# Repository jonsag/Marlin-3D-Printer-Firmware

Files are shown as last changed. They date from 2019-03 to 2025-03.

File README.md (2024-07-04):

# Marlin 3D Printer Firmware

Everything in this repo is for Geeetech I3 Pro B  

*************
Refer to .md file for the Marlin version you want to use.  

Read that file carefully, PLEASE!
*************

## Marlin firmware for my Geeetech i3 Pro B with GT2560A+ board  

Includes BLTouch, T8 lead screws and RepRap Discount Full Graphic Smart Controller.  

I recommend using VSCode for compiling and uploading to printer.  

## Compilation

I use [VS Code](https://code.visualstudio.com/) with [PlatformIO](https://platformio.org/) and [Auto Build Marlin](https://marlinfw.org/docs/basics/auto_build_marlin.html) for compiling, but you can also do this with [Arduino IDE](https://www.arduino.cc/en/software).  

VS Code/PlatformIO instructions [here](<./VSCode, Installation, Compiling and Uploading.md>).  

## Testing and calibrating

View current settings and parameters  
> M503

### BLTouch

#### Set Z offset

View current offset  
> M851 ; view current Z offset

    Send: M851
    Recv: echo:Probe Z Offset: -0.95
    Recv: ok

Heat up bed
> M140 S75 ; set bed temp to 75

Home all axis
> G28 ; home all axis
>
Disable software end stops  
> M211 S0 ; disable software end stops

Do the paper test and bring down Z slowly.  
Note the Z value.  
> M114 ; get current position

Set new offset  
> M851 Z-0.8

    Send: M851 Z-0.8
    Recv: echo:Probe Z Offset: -0.80
    Recv: ok

Save new value to EEPROM  
> M500

You can also adjust the Z offset during prints.  
Double click the knob and adjust the offset until it's OK.  
Then insert new value as above.  

Higher value -> smaller distance from bed  

#### Sensor test

> M280 P0 S10 ; pushes the pin down  
> M280 P0 S90 ; pulls the pin up  
> M280 P0 S120 ; self test – keeps going until you do pin up/down or release alarm  
> M280 P0 S160 ; release alarm  

### PID Tuning

Check current settings  
> M503 ; print all settings stored in eeprom  

    ...
    Recv: echo:; Hotend PID:
    Recv: echo:  M301 P23.12 I1.72 D77.65
    ...  

#### Hotend PID Tuning

Start parts cooler fan  
> M106 S255 ; set parts fan to 100%  

    Send: M106 S255
    Recv: ok

Start tuning  
> M303 E0 S245 C8 ; tune at 245 degrees 8 times  

    ...
    Recv: PID Autotune finished! Put the last Kp, Ki and Kd constants from below into Configuration.h
    Recv: #define DEFAULT_Kp 17.06
    Recv: #define DEFAULT_Ki 1.05
    Recv: #define DEFAULT_Kd 69.18
    ...

Enter new values  
> M301 P17.06 I1.05 D69.18 ; set hotend PID values  

    Send: M301 P17.06 I1.05 D69.18
    Recv: ok

Save to EEPROM  
> M500 ; store to eeprom  

    Send: M500
    Recv: echo:Settings Stored (627 bytes; crc 55228)
    Recv: ok

Stop parts cooler fan  
> M106 S0 ; turn off parts fan

#### Bed PID Tuning

Start tuning  
> M303 E-1 S75 C8 ; tune at 75 degrees 8 times

    ...
    Recv: #define DEFAULT_bedKp 49.22
    Recv: #define DEFAULT_bedKi 9.39
    Recv: #define DEFAULT_bedKd 172.04
    ...

Enter new values  
> M304 P49.22 I9.39 D172.04 ; set bed PID values  

    Recv: ok

Save to EEPROM  
> M500 ; store to eeprom

### Set temperatures

Set extruder temperature  
> M104 S205 ; set temp for default extruder to 205 degrees  

    Send: M104 S205
    Recv: ok

Set bed temperature  
> M140 S65 ; set bed temp to 65 degrees

    Send: M140 S65
    Recv: ok
    ...

### Steps/mm

Show current settings (steps per mm etc)  
> M501

    echo:V47 stored settings retrieved (614 bytes; crc 29566)
    echo:  G21    ; Units in mm
    echo:  M149 C ; Units in Celsius

    echo:Filament settings: Disabled
    echo:  M200 D1.75
    echo:  M200 D0
    echo:Steps per unit:
    echo:  M92 X81.50 Y81.50 Z400.69 E94.00
    echo:Maximum feedrates (units/s):
    echo:  M203 X400.00 Y400.00 Z2.00 E45.00
    echo:Maximum Acceleration (units/s2):
    echo:  M201 X4000 Y4000 Z40 E4000
    echo:Acceleration (units/s2): P<print_accel> R<retract_accel> T<travel_accel>
    echo:  M204 P3000.00 R3000.00 T3000.00
    echo:Advanced: S<min_feedrate> T<min_travel_feedrate> B<min_segment_time_us> X<max_xy_jerk> Z<max_z_jerk> E<max_e_jerk>
    echo:  M205 S0.00 T0.00 B20000 X10.00 Y10.00 Z0.30 E5.00
    echo:Home offset:
    echo:  M206 X0.00 Y0.00 Z0.00
    echo:Auto Bed Leveling:
    echo:  M420 S0
    echo:Material heatup parameters:
    echo:  M145 S0 H180 B70 F0
    echo:  M145 S1 H215 B105 F0
    echo:PID settings:
    echo:  M301 P22.06 I1.06 D114.78
    echo:Z-Probe Offset (mm):
    echo:  M851 Z-0.61 

### Set X/Y center

Home X and Y axes  
> G28 X Y

Set extruder at 0:0  
> G1 X0 Y0

Set extruder at bed center  
> G1 X95 Y96

if bed size is set to 190x192mm in Configuration.h in Marlin firmware  

    // The size of the print bed
    #define X_BED_SIZE 190
    #define Y_BED_SIZE 192

Compensate with  

    #define X_MIN_POS 0
    #define Y_MIN_POS 0
    ...
    #define X_MAX_POS X_BED_SIZE
    #define Y_MAX_POS Y_BED_SIZE

### Homing and leveling

> G28 ; home all axes
> G29 ; do bed leveling

### Set skew factor

Adapted from [https://github.com/MarlinFirmware/Configurations/blob/import-2.0.x/config/examples/Geeetech/Prusa%20i3%20Pro%20B/bltouch/README.md](https://github.com/MarlinFirmware/Configurations/blob/import-2.0.x/config/examples/Geeetech/Prusa%20i3%20Pro%20B/bltouch/README.md)  

The skew factor must be adjusted for each printer:  

First, uncomment `#define XY_SKEW_FACTOR 0.0`, if commented  

      #define XY_SKEW_FACTOR 0.0

Compile and upload the firmware.  
Then, print [YACS (Yet Another Calibration Square)](https://www.thingiverse.com/thing:2563185).  
Hint: scale it considering a margin for brim (if used). The larger, the better to make error measurements.  
Measure the printed part according to the comments in the example configuration file, and set `XY_DIAG_AC`, `XY_DIAG_BD` and `Y_SIDE_AD`.  

      #define XY_DIAG_AC 282.8427124746
      #define XY_DIAG_BD 282.8427124746
      #define XY_SIDE_AD 200
  
Comment `#define XY_SKEW_FACTOR 0.0` again.  

      //#define XY_SKEW_FACTOR 0.0

Compile and upload again.  

## Permissions

Check your permissions.  
You need to belong to the groups tty and dialout to be able to write to the tty/USBx.  

Run  
>$ groups | grep ' tty ' && echo -e "\nGreat! \nYou are a member of 'tty'" || echo -e "\nError: \nYou are not a member of the group 'tty'. \n\nCorrect with 'sudo usermod -a -G tty $USER'"

and  
>$ groups | grep ' dialout ' && echo -e "\nGreat! \nYou are a member of 'dialout'" || echo -e "\nError: \nYou are not a member of the group 'dialout'. \n\nCorrect with 'sudo usermod -a -G dialout $USER'"

to check.  

If you had to add yourself to any group, you must reboot to join the groups.  

>$ sudo reboot

## avrdude

Install avrdude if not installed.  
>$ sudo apt install avrdude

### Upload binary

>$ avrdude -v -q -p m2560 -c wiring -P /dev/ttyUSB0 -D -U flash:w:/path/to/image.hex:i

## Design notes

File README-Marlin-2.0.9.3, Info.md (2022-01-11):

# Firmware Marlin-2.0.9.3 for Geeetech I3 Pro B

Please scroll through whole document so you don't miss anything. :-)  

## Important note - MUST READ

There is a line you HAVE to change in configuration.h before compiling this.  

Uncomment line to disable my skew correction values.  

    #define XY_SKEW_FACTOR 0.0

Comment these out again after you've made the test print and measurements. Read more below.  

(It's not really a disaster if you forget this, but you will get a more skewed print probably.)  

## Other changes for different setups

Below are changes you have to do, if you have a different setup than I have.  

### IF you DON'T have a BLTouch or clone

Comment out line  

    //#define BLTOUCH

### IF you DON'T have T8 lead screws

Comment out line  

    //#define PRO_B_WITH_LEADSCREW

### IF you have the STOCK LCD screen

Comment out line  

    //#define REPRAP_DISCOUNT_FULL_GRAPHIC_SMART_CONTROLLER

and uncomment line  

    #define REPRAP_DISCOUNT_SMART_CONTROLLER

### If you have a BLTouch or clone, not mounted in the same way I have

Check your probe offsets on line  

    #define NOZZLE_TO_PROBE_OFFSET { xx, yy, -zz }

Check offsets on lines  

    #define PROBING_MARGIN_LEFT xx
    #define PROBING_MARGIN_RIGHT xx
    #define PROBING_MARGIN_FRONT yy
    #define PROBING_MARGIN_BACK yy

Check values on line for the "Level Corners" option  

      #define LEVEL_CORNERS_INSET_LFRB { xx, yy, xx, yy } // (mm) Left, Front, Right, Back insets

## Compilation

I use [VS Code](https://code.visualstudio.com/) with [PlatformIO](https://platformio.org/) and [Auto Build Marlin](https://marlinfw.org/docs/basics/auto_build_marlin.html) for compiling, but you can also do this with [Arduino IDE](https://www.arduino.cc/en/software).

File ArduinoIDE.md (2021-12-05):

# Arduino IDE

## Compiling and uploading on Arduino IDE

Download and install Arduino IDE 1.8.x from [https://www.arduino.cc/en/software](https://www.arduino.cc/en/software)  

Open Arduino IDE and open /path/to/Marlin.ini  

Select board:  
    Tools -> Board: ... -> Arduino AVR Boards -> Arduino 2560 or Mega 2560  

Select processor:  
    Tools -> Processor: ... -> ATmega2560 (Mega 2560)  

Set port:  
    Tools -> /dev/ttyUSB0 (or whatever...)  

Select programmer:  
    Tools -> Programmer: ... -> AVRISP  

Compile and upload!  

## Working with binary files

Instead of directly uploading the compiled code with Arduino IDE you can save the compiled code for later upload.  

### Export firmware to binary

Start Arduino IDE and select file and board as above.  

Click 'Sketch -> Export compiled binary'  

The IDE now compiles the firmware to a binary file in the same location as your Marlin.ini.  
It will be called Marlin.ino.mega.hex  

Move the file, and rename it to something sensible.

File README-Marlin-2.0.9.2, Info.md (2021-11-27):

# Firmware Marlin-2.0.9.2 for Geeetech I3 Pro B

Please scroll through whole document so you don't miss anything. :-)  

## Important note - MUST READ

There is a line you HAVE to change in configuration.h before compiling this.  

Uncomment line 1805 to disable my skew correction values.  

    #define XY_SKEW_FACTOR 0.0

Comment these out again after you've made the test print and measurements. Read more below.  

(It's not really a disaster if you forget this, but you will get a more skewed print probably.)  

## Other changes for different setups

Below are changes you have to do, if you have a different setup than I have.  

### IF you DON'T have a BLTouch or clone

Comment out line 1095  

    //#define BLTOUCH

### IF you DON'T have T8 lead screws

Comment out line 930  

    //#define PRO_B_WITH_LEADSCREW

### IF you have the STOCK LCD screen

Comment out line 2376  

    //#define REPRAP_DISCOUNT_FULL_GRAPHIC_SMART_CONTROLLER

and uncomment line 2218  

    #define REPRAP_DISCOUNT_SMART_CONTROLLER

### If you have a BLTouch or clone, not mounted in the same way I have

Check your probe offsets on line 1190  

    #define NOZZLE_TO_PROBE_OFFSET { xx, yy, -zz }

Check offsets on lines 1195-  

    #define PROBING_MARGIN_LEFT xx
    #define PROBING_MARGIN_RIGHT xx
    #define PROBING_MARGIN_FRONT yy
    #define PROBING_MARGIN_BACK yy

Check values on line 1694 for the "Level Corners" option  

      #define LEVEL_CORNERS_INSET_LFRB { xx, yy, xx, yy } // (mm) Left, Front, Right, Back insets

## Compilation

I use [VS Code](https://code.visualstudio.com/) with [PlatformIO](https://platformio.org/) and [Auto Build Marlin](https://marlinfw.org/docs/basics/auto_build_marlin.html) for compiling, but you can also do this with [Arduino IDE](https://www.arduino.cc/en/software).  

## Misc g-code

### Settings

>M503 ; view current settings and parameters
>M500 ; store settings to EEPROM
>M502 ; load settings from EEPROM

### BLTouch

>M280 P0 S10 ; pushes the pin down  
>M280 P0 S90 ; pulls the pin up  
>M280 P0 S120 ; Self test – keeps going until you do pin up/down or release alarm  
>M280 P0 S160 ; Release alarm  

### Homing and leveling

>G28 ; home all axes
>G29 ; do bed leveling

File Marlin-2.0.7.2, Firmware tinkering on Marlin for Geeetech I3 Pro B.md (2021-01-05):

## Firmware tinkering on Marlin-2.0.7.2 for Geeetech I3 Pro B

Further down in this document are instructions on how to trim, set up and install firmware on your printer.  

Please scroll through whole document so you don't miss anything. :-)  

Instructions below are run on a Linux system.  

Important note - MUST READ
==========
There is line you HAVE to change in configuraton.h before compiling this.  

Uncomment line 1454 to disable my skew correction values.  

	#define XY_SKEW_FACTOR 0.0
	
Comment these out again after you've made the test print and measurements. Read more below.  

(It's not really a disaster if you forget this, but you will get a more skewed print probably.)

Other changes for different setups
==========
Below are changes you have to do, if you have a different setup than I have.  

IF you DON'T have a BLTouch or clone
----------
Comment out line 907

	//#define BLTOUCH
	
IF you DON'T have T8 lead screws
----------
Comment out line 744  

	//#define PRO_B_WITH_LEADSCREW
	
IF you have the STOCK LCD screen
---------
Comment out line 2000  

	//#define REPRAP_DISCOUNT_FULL_GRAPHIC_SMART_CONTROLLER
	
and uncomment line 1850  

	#define REPRAP_DISCOUNT_SMART_CONTROLLER
	
If you have a BLTouch or clone, not mounted in the same way I have
----------
Check your probe offsets on line 997  

	#define NOZZLE_TO_PROBE_OFFSET { xx, yy, -zz }
	
Check offsets on lines 1002-  

	#define PROBING_MARGIN_LEFT xx
	#define PROBING_MARGIN_RIGHT xx
	#define PROBING_MARGIN_FRONT yy
	#define PROBING_MARGIN_BACK yy

Check values on line 1386 for the "Level Corners" option  

	  #define LEVEL_CORNERS_INSET_LFRB { xx, yy, xx, yy } // (mm) Left, Front, Right, Back insets

Changes from original firmware release
==========
These are my changes from the source firmware.  
Some things will perhaps have to be adapted to fit your printer setup.  

Makefile
----------
Line 62  

	HARDWARE_MOTHERBOARD ?= 1315
  
>Perhaps not really necessary, but this setting reflects the hardware.
  
configuration.h
----------
Line 73  

	#define STRING_CONFIG_H_AUTHOR "jonsag" // Who made the changes.

> My little mark.
	
130  

	  #define MOTHERBOARD BOARD_GT2560_REV_A_PLUS

>This is essential. Points directly to our hardware setup.
	
134  

	#define CUSTOM_MACHINE_NAME "Geeetech i3 Pro B"

>Puts some text on the display at startup.

426  

	#define TEMP_SENSOR_BED 1
	
>Defines that we have a heated bed, and what type of thermistor.

476  

	#define BED_MAXTEMP      125

>Sets maximum temperature for the heated bed.

498-  

	    #define DEFAULT_Kp_LIST {  22.39,  22.39 }
	    #define DEFAULT_Ki_LIST {   1.91,   1.91 }
	    #define DEFAULT_Kd_LIST { 65.58, 65.58 }

>These are not really used, since we only have one hotend.

502-  

	    #define DEFAULT_Kp  23.12
	    #define DEFAULT_Ki   1.72
	    #define DEFAULT_Kd 77.65

>These are the PID constants that will be used. However I recommend you do a PID tuning as later described.

596  

	//#define THERMAL_PROTECTION_CHAMBER // Enable thermal protection for the heated chamber
	
>If you have a heated and monitored chamber you should uncomment this.

681-  

	#define X_DRIVER_TYPE  A4988
	#define Y_DRIVER_TYPE  A4988
	#define Z_DRIVER_TYPE  A4988

>Not necessary to uncomment, but this now reflects the stock Geeetech drivers.

689  

	#define E0_DRIVER_TYPE A4988

>See above.	

744-  

	#define PRO_B_WITH_LEADSCREW
	#if ENABLED(PRO_B_WITH_LEADSCREW)       // T8 leadscrew version
	  #define DEFAULT_AXIS_STEPS_PER_UNIT   { 81.5, 81.5, 400.69, 108 }
	#else                                   // M8 threaded rod version
	  #define DEFAULT_AXIS_STEPS_PER_UNIT   { 78.74, 78.74, 2560, 105 }
	#endif

> Z steps for T8 lead screws. The added lines are just for conveniance.
	
756  

	#define DEFAULT_MAX_FEEDRATE          { 400, 400, 2, 45 }

>Recommended values. Could be tweaked.

769  

	#define DEFAULT_MAX_ACCELERATION      { 5000, 5000, 50, 5000 }

>See above.

784-  

	#define DEFAULT_ACCELERATION          1000    // X, Y, Z and E acceleration for printing moves
	#define DEFAULT_RETRACT_ACCELERATION  2000    // E acceleration for retracts
	#define DEFAULT_TRAVEL_ACCELERATION   1000    // X, Y, Z acceleration for travel (non printing) moves

>See above.

798  

	 #define DEFAULT_XJERK                 20.0
	 #define DEFAULT_YJERK                 20.0
	 #define DEFAULT_ZJERK                 0.4
  
  >If you enable CLASSIC_JERK on line 796, these are recommended values.  Could be tweaked, but not used now.
  
833  

	#define S_CURVE_ACCELERATION
	
>Better acceleration curve.
	
907-  

	#define BLTOUCH
	#if ENABLED(BLTOUCH)
	  #define BLTOUCH_DELAY 375   // (ms) Enable and increase if 	needed
	#endif

>Essential for BLTouch, and it's clones. Also sets delay.

997  

	#define NOZZLE_TO_PROBE_OFFSET { 20, 2, -0.9}
>The BLTouch's offset from the nozzle. Change these to match your setup.

1002-  

	#define PROBING_MARGIN_LEFT 60
	#define PROBING_MARGIN_RIGHT 0
	#define PROBING_MARGIN_FRONT 0
	#define PROBING_MARGIN_BACK 0

>With these settings I avoid interfering with the clips holding down the glass plate.

1054  

	#define Z_MIN_PROBE_REPEATABILITY_TEST
	
>Enables testing of the repeatability of the level probe.

1101  

	#define INVERT_X_DIR true

>Necessary for our hardware.

1108  

	#define INVERT_E0_DIR true

>See above.
	
1137-  

	#define X_BED_SIZE 186
	#define Y_BED_SIZE 167

>We could adjust this, but now I avoid interferring with the glass bed clamps.
	
1141-  

	#define X_MIN_POS 10
	#define Y_MIN_POS -10

>See above.

1144-  

	#define X_MAX_POS (X_MIN_POS + X_BED_SIZE)
	#define Y_MAX_POS (-Y_MIN_POS + Y_BED_SIZE))
	#define Z_MAX_POS 185

>This is the conclusion of the above settings.
	
1248  

	#define AUTO_BED_LEVELING_LINEAR
	
>You could also uncomment line 1249 instead, or one of the other measurement types. This makes most sense to me.
	
1257  

	#define RESTORE_LEVELING_AFTER_G28
	
>Keeps the leveling data after a G28 home command.

1296  

	#define GRID_MAX_POINTS_X 3
	
>The number of probes in both directions. The value squared is the total number of probes.

1306  

	#define EXTRAPOLATE_BEYOND_GRID

>If you went with bilinear probong above, this is a good setting.
 
1326  

	  #define MESH_EDIT_GFX_OVERLAY   // Display a graphics overlay while editing the mesh

>For unified bed leveling this is a nice feature.

1356  

	#define LCD_BED_LEVELING

>Adds an extra option on how to level the bed.
	
1365  

	#define LEVEL_BED_CORNERS

>A nice feature for do some basic manual leveling.
 
1368  

	  #define LEVEL_CORNERS_INSET_LFRB { 35, 10, 15, 20 } // (mm) Left, Front, Right, Back insets

>Keeps the hotend away from the clamps.

1371  

	  #define LEVEL_CENTER_TOO              // Move to the center after the last corner

>Stop at center when doing the corners.
 
1400  

	#define Z_SAFE_HOMING

>Don't let the probe get outside the bed.
	
1444  

	#define SKEW_CORRECTION

>Enabling this lets your firmware make correctionsto your printer setup. If your axes are not completely perpendicular to each other, which they seldom are, these will be corrected. Read below on how to do this.

1448  

	  #define XY_DIAG_AC 143.55 //142.90 // should be 143.754808615 //282.8427124746
	  #define XY_DIAG_BD 143.95 //143.10 //282.8427124746
	  #define XY_SIDE_AD 101.65
  
>These are MY values AFTER I've done the test print and measuring. You will have enter YOUR values.

1454  

	  //#define XY_SKEW_FACTOR 0.0
	  
>Comment this AFTER you've done the test print and measurements.
 
1468  

	  #define SKEW_CORRECTION_GCODE

>Extra feature for skew correction.
 
1486-  

	#define EEPROM_SETTINGS     // Persistent storage with M500 and M501

>Enables storing of settings with G-code.
	
1518  

	#define PREHEAT_1_TEMP_HOTEND 200
	#define PREHEAT_1_TEMP_BED     65

>Enter whatever values are handy for you.
	
1522  

	#define PREHEAT_2_LABEL       "PETG"
	#define PREHEAT_2_TEMP_HOTEND 235
	#define PREHEAT_2_TEMP_BED    85

>See above.

1739  

	#define SDSUPPORT

>We do have an SD card reader.

1756  

	#define SD_CHECK_AND_RETRY

>This setting makes sense.

1819  

	#define INDIVIDUAL_AXIS_HOMING_MENU

>Handy option to have.
	
1827  

	#define SPEAKER

>Our speaker is capable of putting out some different sounds.

1836-  

	#define LCD_FEEDBACK_FREQUENCY_DURATION_MS 4
	#define LCD_FEEDBACK_FREQUENCY_HZ 5000

>I think button press beeps are nice.

2000  

	#define REPRAP_DISCOUNT_SMART_CONTROLLER

>I have upgraded my printer with this full graphic LCD. If you still have the stock control panel, enable line 1850 instead.
	
Other possible changes in configuration.h
==========

Extra probing
----------
1025  

	#define MULTIPLE_PROBING 3

Compiling and uploading on Arduino IDE
==========
Download and install Arduino IDE 1.8.x from https://www.arduino.cc/en/software  

Open Arduino IDE and open /path/to/Marlin.ini  

Select board:  
Tools -> Board: ... -> Arduino AVR Boards -> Arduino 2560 or Mega 2560  

Select processor:  
Tools -> Processor: ... -> ATmega2560 (Mega 2560)  
 
 Set port:  
Tools -> /dev/ttyUSB0 or whatever...  

Select programmer:  
Tools -> Programmer: ... -> AVRIPS mkII  

Compile and upload!  

Permissions
==========
Check your permissions. You need to belong to the groups tty and dialout to be able to write to the tty/USB.  

Run  
>$ groups | grep ' tty ' && echo -e "\nGreat! \nYou are a member of 'tty'" || echo -e "\nError: \nYou are not a member of the group 'tty'. \n\nCorrect with 'sudo usermod -a -G tty $USER'"

and  
>$ groups | grep ' dialout ' && echo -e "\nGreat! \nYou are a member of 'dialout'" || echo -e "\nError: \nYou are not a member of the group 'dialout'. \n\nCorrect with 'sudo usermod -a -G dialout $USER'"

to check.  

If you had to add yourself to any group, you must reboot to join the groups.  

>$ sudo reboot

Working with binary files
==========
Instead of directly uploading the compiled code with Arduino IDE you can save the compiled code for later upload.  

Export firmware to binary
----------
 Start Arduino IDE and select file and board as above.  

Click 'Sketch -> Export compiled binary'  

The IDE now compiles the firmware to a binary file in the same location as your Marlin.ini.  
It will be called Marlin.ino.mega.hex  

Move the file, and rename it to something sensible.  

avrdude
----------
Install avrdude if not installed.  
>$ sudo apt install avrdude

avrdude is already a part of the Arduino IDE, but this makes it easier to run.  

Upload binary
----------
>$ avrdude -v -q -p m2560 -c wiring -P /dev/ttyUSB0 -D -U flash:w:/path/to/image.hex:i

Configuration after upload
==========

PID tuning
---------------
Start parts fan at 100%  
>M106 S255

	[...]
	Send: M106 S255
	Recv: ok
	[...]

Start tuning  
>M303 E0 S205 C8

	[...]
	Recv:  bias: 169 d: 85 min: 202.71 max: 207.81 Ku: 42.41 Tu: 27.20
	Recv:  Classic PID
	Recv:  Kp: 25.44 Ki: 1.87 Kd: 86.50
	Recv: PID Autotune finished! Put the last Kp, Ki and Kd constants from below into Configuration.h
	Recv: #define DEFAULT_Kp 25.44
	Recv: #define DEFAULT_Ki 1.87
	Recv: #define DEFAULT_Kd 86.50
	Recv: ok
	[...]
	
Enter new values  
>M301 P25.44 I1.87 D86.50

	[...]
	Send: M301 P25.44 I1.87 D86.50
	Recv: echo: p:25.44 i:1.87 d:86.50
	Recv: ok
	[...]
	
Save to EEPROM  
>M500

	[...]
	Send: M500
	Recv: echo:Settings Stored (657 bytes; crc 43001)
	Recv: ok
	[...]

Set Z-offset
---------------
View current offset  
>M851

	[...]
	Send: M851
	Recv: Probe Offset X20.00 Y2.00 Z-0.90
	Recv: ok
	[...]
	
Set new Z offset  
>M851 Z-0.8

	[...]
	Send: M851 Z-0.8
	Recv: echo:Probe Z Offset: -0.80
	Recv: ok
	[...]
		
Save new value to EEPROM  
>M500

Higher value -> smaller distance from bed  
The above example will decrease the distance from the bed, ie. the gap between nozzle and bed will be smaller.  

This can of course also be done from the LCD-display.  

Skew factor
----------
Adapted from https://github.com/MarlinFirmware/Configurations/blob/import-2.0.x/config/examples/Geeetech/Prusa%20i3%20Pro%20B/bltouch/README.md  

The skew factor must be adjusted for each printer:

- First, uncomment `#define XY_SKEW_FACTOR 0.0`, if commented

1445  

	  #define XY_SKEW_FACTOR 0.0

- Compile and upload the firmware.
- Then, print [YACS (Yet Another Calibration Square)](https://www.thingiverse.com/thing:2563185). Hint, scale it considering a margin for brim (if used). The larger, the better to make error measurements.
- Measure the printed part according to the comments in the example configuration file, and set `XY_DIAG_AC`, `XY_DIAG_BD` and `Y_SIDE_AD`.

1439  

	  #define XY_DIAG_AC 282.8427124746
	  #define XY_DIAG_BD 282.8427124746
	  #define XY_SIDE_AD 200
	  
- Comment `#define XY_SKEW_FACTOR 0.0` again.
	
1445  

	  //#define XY_SKEW_FACTOR 0.0

- Compile and upload again.

Misc g-code
==========
Settings
----------
>M503 ; view current settings and parameters

>M500 ; store settings to EEPROM

>M502 ; load settings from EEPROM

BLTouch
---------------
>M280 P0 S10 ; pushes the pin down  

>M280 P0 S90 ; pulls the pin up  

>M280 P0 S120 ; Self test – keeps going until you do pin up/down or release alarm  

>M280 P0 S160 ; Release alarm  

Homing and leveling
----------
>G28 ; home all axes

>G29 ; do bed leveling

Below is just for my own reference
==========
Other PID values I've tried:  
>M301 P32.86 I2.59 D104.31 ; 1.1.8, with fan off
>M301 P33.26 I2.49 D111.03 ; 2.0.7.2, with fan off
>M301 P28.44 I2.12 D95.53 ; 2.0.7.2, fan on
>M301 P23.26 I1.72 D78.61 ; 2.0.7.2, fan off, 200 degrees
>M301 P23.12 I1.72 D77.65 ; 2.0.7.2, fan on, 200 degrees

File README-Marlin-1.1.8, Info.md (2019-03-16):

#Firmware tinkering on Marlin for Geeetech I3 Pro B

Configuration.h
===============

Motherboard selection, 119-123
---------------
	// The following define selects which electronics board you have.
	// Please choose the name from boards.h that matches your setup
	#ifndef MOTHERBOARD
	  #define MOTHERBOARD BOARD_GT2560_REV_A_PLUS
	#endif
	
Custom name, 125-127
---------------
	// Optional custom name for your RepStrap or other custom machine
	// Displayed in the LCD "Ready" message
	#define CUSTOM_MACHINE_NAME "Geeetech i3 Pro B"

Filament diameter, 139-140
---------------
	// Generally expected filament diameter (1.75, 2.85, 3.0, ...). Used for Volumetric, Filament Width Sensor, etc.
	#define DEFAULT_NOMINAL_FILAMENT_DIA 1.75

Temperature sensors, 243-294
---------------
	/**
	 * --NORMAL IS 4.7kohm PULLUP!-- 1kohm pullup can be used on hotend sensor, using correct resistor and table
	 *
	 * Temperature sensors available:
	...
	...
	...
	 */
	#define TEMP_SENSOR_0 1
	#define TEMP_SENSOR_1 0
	#define TEMP_SENSOR_2 0
	#define TEMP_SENSOR_3 0
	#define TEMP_SENSOR_4 0
	#define TEMP_SENSOR_BED 1
	
Min temps, 315-323
---------------
	// The minimal temperature defines the temperature below which the heater will not be enabled It is used
	// to check that the wiring to the thermistor is not broken.
	// Otherwise this would lead to the heater being powered on all the time.
	#define HEATER_0_MINTEMP 8
	#define HEATER_1_MINTEMP 5
	#define HEATER_2_MINTEMP 5
	#define HEATER_3_MINTEMP 5
	#define HEATER_4_MINTEMP 5
	#define BED_MINTEMP 8

Steps/mm, 527-533
---------------
	/**
	 * Default Axis Steps Per Unit (steps/mm)
	 * Override with M92
	 *                                      X, Y, Z, E0 [, E1[, E2[, E3[, E4]]]]
	 */
	//#define DEFAULT_AXIS_STEPS_PER_UNIT   { 81.5, 81.5, 2577.46, 94 }
	#define DEFAULT_AXIS_STEPS_PER_UNIT   { 81.5, 81.5, 400.69, 93 }

Max feed rate, 534-539
---------------
	/**
	 * Default Max Feed Rate (mm/s)
	 * Override with M203
	 *                                      X, Y, Z, E0 [, E1[, E2[, E3[, E4]]]]
	 */
	#define DEFAULT_MAX_FEEDRATE          { 400, 400, 2, 45 }

Max accceleration, 541-547
---------------
	/**
	 * Default Max Acceleration (change/s) change = mm/s
	 * (Maximum start speed for accelerated moves)
	 * Override with M201
	 *                                      X, Y, Z, E0 [, E1[, E2[, E3[, E4]]]]
	 */
	#define DEFAULT_MAX_ACCELERATION      { 5000, 5000, 50, 5000 }

Default acceleration, 549-559
---------------
	/**
	 * Default Acceleration (change/s) change = mm/s
	 * Override with M204
	 *
	 *   M204 P    Acceleration
	 *   M204 R    Retract Acceleration
	 *   M204 T    Travel Acceleration
	 */
	#define DEFAULT_ACCELERATION          1000    // X, Y, Z and E acceleration for printing moves
	#define DEFAULT_RETRACT_ACCELERATION  2000    // E acceleration for retracts
	#define DEFAULT_TRAVEL_ACCELERATION   1000    // X, Y, Z acceleration for travel (non printing) moves

Default jerk, 572-561
---------------
	/**
	 * Default Jerk (mm/s)
	 * Override with M205 X Y Z E
	 *
	 * "Jerk" specifies the minimum speed change that requires acceleration.
	 * When changing speed and direction, if the difference is less than the
	 * value set here, it may happen instantaneously.
	 */
	#define DEFAULT_XJERK                 20.0
	#define DEFAULT_YJERK                 20.0
	#define DEFAULT_ZJERK                  0.4
	#define DEFAULT_EJERK                  5.0
	
Bltouch, 637-643
---------------
	/**
	 * The BLTouch probe uses a Hall effect sensor and emulates a servo.
	 */
	#define BLTOUCH
	#if ENABLED(BLTOUCH)
	  #define BLTOUCH_DELAY 375   // (ms) Enable and increase if needed
	#endif

Bltouch probe offsets, 667-688
---------------
	/**
	 *   Z Probe to nozzle (X,Y) offset, relative to (0, 0).
	 *   X and Y offsets must be integers.
	 *
	 *   In the following example the X and Y offsets are both positive:
	 *   #define X_PROBE_OFFSET_FROM_EXTRUDER 10
	 *   #define Y_PROBE_OFFSET_FROM_EXTRUDER 10
	 *
	 *      +-- BACK ---+
	 *      |           |
	 *    L |    (+) P  | R <-- probe (20,20)
	 *    E |           | I
	 *    F | (-) N (+) | G <-- nozzle (10,10)
	 *    T |           | H
	 *      |    (-)    | T
	 *      |           |
	 *      O-- FRONT --+
	 *    (0,0)
	 */
	#define X_PROBE_OFFSET_FROM_EXTRUDER -40  // X offset: -left  +right  [of the nozzle]
	#define Y_PROBE_OFFSET_FROM_EXTRUDER -0  // Y offset: -front +behind [the nozzle]
	#define Z_PROBE_OFFSET_FROM_EXTRUDER -0.9  // Z offset: -below +above  [the nozzle]

Z clearance, 704-719
---------------
	/**
	 * Z probes require clearance when deploying, stowing, and moving between
	 * probe points to avoid hitting the bed and other hardware.
	 * Servo-mounted probes require extra space for the arm to rotate.
	 * Inductive probes need space to keep from triggering early.
	 *
	 * Use these settings to specify the distance (mm) to raise the probe (or
	 * lower the bed). The values set here apply over and above any (negative)
	 * probe Z Offset set with Z_PROBE_OFFSET_FROM_EXTRUDER, M851, or the LCD.
	 * Only integer values >= 1 are valid here.
	 *
	 * Example: `M851 Z-5` with a CLEARANCE of 4  =>  9mm from bed to nozzle.
	 *     But: `M851 Z+1` with a CLEARANCE of 2  =>  2mm from bed to nozzle.
	 */
	#define Z_CLEARANCE_DEPLOY_PROBE   5 // Z Clearance for Deploy/Stow
	#define Z_CLEARANCE_BETWEEN_PROBES  5 // Z Clearance between probe point
	
Stepper directions, 750-765
---------------
		// Invert the stepper direction. Change (or reverse the motor connector) if an axis goes the wrong way.
	#define INVERT_X_DIR true
	#define INVERT_Y_DIR true
	#define INVERT_Z_DIR false

	// Enable this option for Toshiba stepper drivers
	//#define CONFIG_STEPPERS_TOSHIBA

	// @section extruder

	// For direct drive extruder v9 set to true, for geared extruder set to false.
	#define INVERT_E0_DIR true
	#define INVERT_E1_DIR false
	#define INVERT_E2_DIR false
	#define INVERT_E3_DIR false
	#define INVERT_E4_DIR false
	
Bed size and travel limits, 782-792
---------------

	// The size of the print bed
	#define X_BED_SIZE 196
	#define Y_BED_SIZE 192

	// Travel limits (mm) after homing, corresponding to endstop positions.
	#define X_MIN_POS 5
	#define Y_MIN_POS 0
	#define Z_MIN_POS 0
	#define X_MAX_POS X_BED_SIZE + X_MIN_POS
	#define Y_MAX_POS Y_BED_SIZE
	#define Z_MAX_POS 185
	
Bed levelling, 839-876
---------------
	/**
	 * Choose one of the options below to enable G29 Bed Leveling. The parameters
	 * and behavior of G29 will change depending on your selection.
	 *
	 *  If using a Probe for Z Homing, enable Z_SAFE_HOMING also!
	...
	...
	...
	//#define AUTO_BED_LEVELING_3POINT
	#define AUTO_BED_LEVELING_LINEAR
	//#define AUTO_BED_LEVELING_BILINEAR
	//#define AUTO_BED_LEVELING_UBL
	//#define MESH_BED_LEVELING

Bed levelling options, 912-923
---------------

	  // Set the number of grid points per dimension.
	  #define GRID_MAX_POINTS_X 3
	  #define GRID_MAX_POINTS_Y GRID_MAX_POINTS_X

	  // Set the boundaries for probing (where the probe can reach).
	  #define LEFT_PROBE_BED_POSITION 10
	  #define RIGHT_PROBE_BED_POSITION 150
	  #define FRONT_PROBE_BED_POSITION 10
	  #define BACK_PROBE_BED_POSITION 190

	  // The Z probe minimum outer margin (to validate G29 parameters).
	  #define MIN_PROBE_EDGE 8

Move between bed corners, 1004-1005
---------------
	// Add a menu item to move between bed corners for manual bed adjustment
	#define LEVEL_BED_CORNERS

Z safe homing, 1025-1034
---------------
	// Use "Z Safe Homing" to avoid homing with a Z probe outside the bed area.
	//
	// With this feature enabled:
	//
	// - Allow Z homing only after X and Y homing AND stepper drivers still enabled.
	// - If stepper drivers time out, it will need X and Y homing again before Z homing.
	// - Move the Z probe (or nozzle) to a defined XY point before Z Homing when homing all axes (G28).
	// - Prevent Z homing when the Z probe is outside bed area.
	//
	#define Z_SAFE_HOMING

M500 and M501 commands, 1111-1118
---------------
	// The microcontroller can store settings in the EEPROM, e.g. max velocity...
	// M500 - stores parameters in EEPROM
	// M501 - reads parameters from EEPROM (if you need reset them after you changed them temporarily).
	// M502 - reverts to the default "factory settings".  You still need to store them in EEPROM afterwards if you want to.
	//
	#define EEPROM_SETTINGS // Enable for M500 and M501 commands

Preheating, 1147-1154
---------------
	// Preheat Constants
	#define PREHEAT_1_TEMP_HOTEND 180
	#define PREHEAT_1_TEMP_BED     70
	#define PREHEAT_1_FAN_SPEED     0 // Value from 0 to 255

	#define PREHEAT_2_TEMP_HOTEND 225
	#define PREHEAT_2_TEMP_BED    90
	#define PREHEAT_2_FAN_SPEED     0 // Value from 0 to 255

SD support, 1325-1332
---------------
	/**
	 * SD CARD
	 *
	 * SD Card support is disabled by default. If your controller has an SD slot,
	 * you must uncomment the following option or it won't work.
	 *
	 */
	#define SDSUPPORT

Feedback sound, 1405-1413
---------------
	//
	// The duration and frequency for the UI feedback sound.
	// Set these to 0 to disable audio feedback in the LCD menus.
	//
	// Note: Test audio output with the G-Code:
	//  M300 S<frequency Hz> P<duration ms>
	//
	#define LCD_FEEDBACK_FREQUENCY_DURATION_MS 0
	#define LCD_FEEDBACK_FREQUENCY_HZ 0

Smart controller, 1464-1470
---------------
	//
	// RepRapDiscount Smart Controller.
	// http://reprap.org/wiki/RepRapDiscount_Smart_Controller
	//
	// Note: Usually sold with a white PCB.
	//
	#define REPRAP_DISCOUNT_SMART_CONTROLLER

Marlin_main.cpp
===============

Line 13206
---------------
	        planner.buffer_line(delta[A_AXIS], delta[B_AXIS], raw[Z_AXIS], raw[E_AXIS], _feedrate_mm_s, active_extruder);

Version.h
===============

pins_GT2560_REV_A_PLUS.h
===============

Bltouch, 31-35
---------------
	#if ENABLED(BLTOUCH)
	  #define SERVO0_PIN  11
	#else
	  #define SERVO0_PIN  11
	#endif

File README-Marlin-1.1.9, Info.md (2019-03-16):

#Firmware tinkering on Marlin for Geeetech I3 Pro B

Configuration.h
===============

Motherboard selection, 131-135
---------------
	// The following define selects which electronics board you have.
	// Please choose the name from boards.h that matches your setup
	#ifndef MOTHERBOARD
	  #define MOTHERBOARD BOARD_GT2560_REV_A_PLUS
	#endif
	
Custom name, 137-139
---------------
	// Optional custom name for your RepStrap or other custom machine
	// Displayed in the LCD "Ready" message
	#define CUSTOM_MACHINE_NAME "Geeetech I3 Pro B""

Filament diameter, 151-152
---------------
	// Generally expected filament diameter (1.75, 2.85, 3.0, ...). Used for Volumetric, Filament Width Sensor, etc.
	#define DEFAULT_NOMINAL_FILAMENT_DIA 1.75

Temperature sensors, 264-319
---------------
	/**
	 * --NORMAL IS 4.7kohm PULLUP!-- 1kohm pullup can be used on hotend sensor, using correct resistor and table
	 *
	 * Temperature sensors available:
	...
	...
	...
	 */
	#define TEMP_SENSOR_0 1
	#define TEMP_SENSOR_1 0
	#define TEMP_SENSOR_2 0
	#define TEMP_SENSOR_3 0
	#define TEMP_SENSOR_4 0
	#define TEMP_SENSOR_BED 1
	#define TEMP_SENSOR_CHAMBER 0
	
Min temps, 340-348
---------------
	// The minimal temperature defines the temperature below which the heater will not be enabled It is used
	// to check that the wiring to the thermistor is not broken.
	// Otherwise this would lead to the heater being powered on all the time.
	#define HEATER_0_MINTEMP 8
	#define HEATER_1_MINTEMP 5
	#define HEATER_2_MINTEMP 5
	#define HEATER_3_MINTEMP 5
	#define HEATER_4_MINTEMP 5
	#define BED_MINTEMP 8

Steps/mm, 606-611
---------------
	/**
	 * Default Axis Steps Per Unit (steps/mm)
	 * Override with M92
	 *                                      X, Y, Z, E0 [, E1[, E2[, E3[, E4]]]]
	 */
	#define DEFAULT_AXIS_STEPS_PER_UNIT   { 81.5, 81.5, 400.69, 108 }
	
Max feed rate, 613-618
---------------
	/**
	 * Default Max Feed Rate (mm/s)
	 * Override with M203
	 *                                      X, Y, Z, E0 [, E1[, E2[, E3[, E4]]]]
	 */
	#define DEFAULT_MAX_FEEDRATE          { 400, 400, 2, 45 }
	
Max accceleration, 620-626
---------------
	/**
	 * Default Max Acceleration (change/s) change = mm/s
	 * (Maximum start speed for accelerated moves)
	 * Override with M201
	 *                                      X, Y, Z, E0 [, E1[, E2[, E3[, E4]]]]
	 */
	#define DEFAULT_MAX_ACCELERATION      { 5000, 5000, 50, 5000 }
	
Default acceleration, 628-638
---------------
	/**
	 * Default Acceleration (change/s) change = mm/s
	 * Override with M204
	 *
	 *   M204 P    Acceleration
	 *   M204 R    Retract Acceleration
	 *   M204 T    Travel Acceleration
	 */
	#define DEFAULT_ACCELERATION          1000    // X, Y, Z and E acceleration for printing moves
	#define DEFAULT_RETRACT_ACCELERATION  2000    // E acceleration for retracts
	#define DEFAULT_TRAVEL_ACCELERATION   1000    // X, Y, Z acceleration for travel (non printing) moves

Default jerk, 640-651
---------------
	/**
	 * Default Jerk (mm/s)
	 * Override with M205 X Y Z E
	 *
	 * "Jerk" specifies the minimum speed change that requires acceleration.
	 * When changing speed and direction, if the difference is less than the
	 * value set here, it may happen instantaneously.
	 */
	#define DEFAULT_XJERK                 20.0
	#define DEFAULT_YJERK                 20.0
	#define DEFAULT_ZJERK                 0.4
	#define DEFAULT_EJERK                 5.0
	
Bltouch, 727-733
---------------
	/**
	 * The BLTouch probe uses a Hall effect sensor and emulates a servo.
	 */
	#define BLTOUCH
	#if ENABLED(BLTOUCH)
	  #define BLTOUCH_DELAY 375   // (ms) Enable and increase if needed
	#endif

Bltouch probe offsets, 760-781
---------------	
	/**
	 *   Z Probe to nozzle (X,Y) offset, relative to (0, 0).
	 *   X and Y offsets must be integers.
	 *
	 *   In the following example the X and Y offsets are both positive:
	 *   #define X_PROBE_OFFSET_FROM_EXTRUDER 10
	 *   #define Y_PROBE_OFFSET_FROM_EXTRUDER 10
	 *
	 *      +-- BACK ---+
	 *      |           |
	 *    L |    (+) P  | R <-- probe (20,20)
	 *    E |           | I
	 *    F | (-) N (+) | G <-- nozzle (10,10)
	 *    T |           | H
	 *      |    (-)    | T
	 *      |           |
	 *      O-- FRONT --+
	 *    (0,0)
	 */
	#define X_PROBE_OFFSET_FROM_EXTRUDER -40  // X offset: -left  +right  [of the nozzle]
	#define Y_PROBE_OFFSET_FROM_EXTRUDER 0  // Y offset: -front +behind [the nozzle]
	#define Z_PROBE_OFFSET_FROM_EXTRUDER -0.9   // Z offset: -below +above  [the nozzle]

Speed between probes, 786-787
---------------
	// X and Y axis travel speed (mm/m) between probes
	#define XY_PROBE_SPEED 8000

Feedrate for probing, 792-793
---------------
	// Feedrate (mm/m) for the "accurate" probe of each point
	#define Z_PROBE_SPEED_SLOW (Z_PROBE_SPEED_FAST )

Z clearance, 800-817
---------------
	/**
	 * Z probes require clearance when deploying, stowing, and moving between
	 * probe points to avoid hitting the bed and other hardware.
	 * Servo-mounted probes require extra space for the arm to rotate.
	 * Inductive probes need space to keep from triggering early.
	 *
	 * Use these settings to specify the distance (mm) to raise the probe (or
	 * lower the bed). The values set here apply over and above any (negative)
	 * probe Z Offset set with Z_PROBE_OFFSET_FROM_EXTRUDER, M851, or the LCD.
	 * Only integer values >= 1 are valid here.
	 *
	 * Example: `M851 Z-5` with a CLEARANCE of 4  =>  9mm from bed to nozzle.
	 *     But: `M851 Z+1` with a CLEARANCE of 2  =>  2mm from bed to nozzle.
	 */
	#define Z_CLEARANCE_DEPLOY_PROBE   3 // Z Clearance for Deploy/Stow
	#define Z_CLEARANCE_BETWEEN_PROBES 2 // Z Clearance between probe points
	#define Z_CLEARANCE_MULTI_PROBE    2 // Z Clearance between multiple probes
	#define Z_AFTER_PROBING            5 // Z position after probing is done

Stepper directions, 850-862
---------------
	// Invert the stepper direction. Change (or reverse the motor connector) if an axis goes the wrong way.
	#define INVERT_X_DIR true
	#define INVERT_Y_DIR true
	#define INVERT_Z_DIR false

	// @section extruder

	// For direct drive extruder v9 set to true, for geared extruder set to false.
	#define INVERT_E0_DIR true
	#define INVERT_E1_DIR false
	#define INVERT_E2_DIR false
	#define INVERT_E3_DIR false
	#define INVERT_E4_DIR false
	
Bed size and travel limits, 881-891
---------------
	// The size of the print bed
	#define X_BED_SIZE 196
	#define Y_BED_SIZE 192

	// Travel limits (mm) after homing, corresponding to endstop positions.
	#define X_MIN_POS 5
	#define Y_MIN_POS 0
	#define Z_MIN_POS 0
	#define X_MAX_POS X_BED_SIZE + X_MIN_POS
	#define Y_MAX_POS Y_BED_SIZE
	#define Z_MAX_POS 185
	
Bed levelling, 943-980
---------------
	/**
	 * Choose one of the options below to enable G29 Bed Leveling. The parameters
	 * and behavior of G29 will change depending on your selection.
	 *
	 *  If using a Probe for Z Homing, enable Z_SAFE_HOMING also!
	...
	...
	...
	//#define AUTO_BED_LEVELING_3POINT
	#define AUTO_BED_LEVELING_LINEAR
	//#define AUTO_BED_LEVELING_BILINEAR
	//#define AUTO_BED_LEVELING_UBL
	//#define MESH_BED_LEVELING
	
Leveling disabled, 982-986
---------------
	/**
	 * Normally G28 leaves leveling disabled on completion. Enable
	 * this option to have G28 restore the prior leveling state.
	 */
	#define RESTORE_LEVELING_AFTER_G28

Enable mesh validation, 1007-1016
---------------
	  /**
	   * Enable the G26 Mesh Validation Pattern tool.
	   */
	  #define G26_MESH_VALIDATION
	  #if ENABLED(G26_MESH_VALIDATION)
	    #define MESH_TEST_NOZZLE_SIZE    0.4  // (mm) Diameter of primary nozzle.
	    #define MESH_TEST_LAYER_HEIGHT   1.5  // (mm) Default layer height for the G26 Mesh Validation Tool.
	    #define MESH_TEST_HOTEND_TEMP  230.0  // (°C) Default nozzle temperature for the G26 Mesh Validation Tool.
	    #define MESH_TEST_BED_TEMP      80.0  // (°C) Default bed temperature for the G26 Mesh Validation Tool.
	  #endif

Options for linear leveling, 1020-1052
---------------
	#if ENABLED(AUTO_BED_LEVELING_LINEAR) || ENABLED(AUTO_BED_LEVELING_BILINEAR)

	  // Set the number of grid points per dimension.
	  #define GRID_MAX_POINTS_X 3
	  #define GRID_MAX_POINTS_Y GRID_MAX_POINTS_X

	  // Set the boundaries for probing (where the probe can reach).
	  #define LEFT_PROBE_BED_POSITION 10
	  #define RIGHT_PROBE_BED_POSITION (X_BED_SIZE - MIN_PROBE_EDGE - X_PROBE_OFFSET_FROM_EXTRUDER) 
	  #define FRONT_PROBE_BED_POSITION 10
	  //#define BACK_PROBE_BED_POSITION 143
	  #define BACK_PROBE_BED_POSITION (Y_BED_SIZE - MIN_PROBE_EDGE + Y_PROBE_OFFSET_FROM_EXTRUDER -3)

	  // Probe along the Y axis, advancing X after each column
	  //#define PROBE_Y_FIRST

	  #if ENABLED(AUTO_BED_LEVELING_BILINEAR)

	    // Beyond the probed grid, continue the implied tilt?
	    // Default is to maintain the height of the nearest edge.
	    #define EXTRAPOLATE_BEYOND_GRID

	    //
	    // Experimental Subdivision of the grid by Catmull-Rom method.
	    // Synthesizes intermediate points to produce a more detailed mesh.
	    //
	    //#define ABL_BILINEAR_SUBDIVISION
	    #if ENABLED(ABL_BILINEAR_SUBDIVISION)
	      // Number of subdivisions between probe points
	      #define BILINEAR_SUBDIVISIONS 3
	    #endif

	  #endif

Level bed corners, 1013-1017
---------------
	#if ENABLED(LEVEL_BED_CORNERS)
	  #define LEVEL_CORNERS_INSET 30    // (mm) An inset for corner leveling
	  #define LEVEL_CORNERS_Z_HOP  4.0  // (mm) Move nozzle up before moving between corners
	  //#define LEVEL_CENTER_TOO        // Move to the center after the last corner
	#endif

Z safe homing, 1137-1156
---------------
	// Use "Z Safe Homing" to avoid homing with a Z probe outside the bed area.
	//
	// With this feature enabled:
	//
	// - Allow Z homing only after X and Y homing AND stepper drivers still enabled.
	// - If stepper drivers time out, it will need X and Y homing again before Z homing.
	// - Move the Z probe (or nozzle) to a defined XY point before Z Homing when homing all axes (G28).
	// - Prevent Z homing when the Z probe is outside bed area.
	//
	#define Z_SAFE_HOMING
	
Homing speeds, 1153-1155
---------------
	// Homing speeds (mm/m)
	#define HOMING_FEEDRATE_XY (60*60)
	#define HOMING_FEEDRATE_Z  (60*60)

M500 and M501 commands, 1221-1230
---------------
	// EEPROM
	//
	// The microcontroller can store settings in the EEPROM, e.g. max velocity...
	// M500 - stores parameters in EEPROM
	// M501 - reads parameters from EEPROM (if you need reset them after you changed them temporarily).
	// M502 - reverts to the default "factory settings".  You still need to store them in EEPROM afterwards if you want to.
	//
	#define EEPROM_SETTINGS // Enable for M500 and M501 commands
	//#define DISABLE_M503    // Saves ~2700 bytes of PROGMEM. Disable for release!
	#define EEPROM_CHITCHAT   // Give feedback on EEPROM commands. Disable to save PROGMEM.

Host keepalive, 1233-1240
---------------
	// Host Keepalive
	//
	// When enabled Marlin will send a busy status message to the host
	// every couple of seconds when it can't accept commands.
	//
	#define HOST_KEEPALIVE_FEATURE        // Disable this if your host doesn't like keepalive messages
	#define DEFAULT_KEEPALIVE_INTERVAL 4  // Number of seconds between "busy" messages. Set with M113.
	#define BUSY_WHILE_HEATING            // Some hosts require "busy" messages even during heating

Preheating, 2559-1266
---------------
	// Preheat Constants
	#define PREHEAT_1_TEMP_HOTEND 180
	#define PREHEAT_1_TEMP_BED     60
	#define PREHEAT_1_FAN_SPEED     0 // Value from 0 to 255

	#define PREHEAT_2_TEMP_HOTEND 225
	#define PREHEAT_2_TEMP_BED    90
	#define PREHEAT_2_FAN_SPEED     0 // Value from 0 to 255
	
Nozzle park, 1281-1286
---------------
	#if ENABLED(NOZZLE_PARK_FEATURE)
	  // Specify a park position as { X, Y, Z }
	  #define NOZZLE_PARK_POINT { (X_MIN_POS + 10), (Y_MAX_POS - 10), 20 }
	  #define NOZZLE_PARK_XY_FEEDRATE 100   // X and Y axes feedrate in mm/s (also used for delta printers Z axis)
	  #define NOZZLE_PARK_Z_FEEDRATE 100      // Z axis feedrate in mm/s (not used for delta printers)
	#endif

SD support, 1424-1431
---------------
	/**
	 * SD CARD
	 *
	 * SD Card support is disabled by default. If your controller has an SD slot,
	 * you must uncomment the following option or it won't work.
	 *
	 */
	#define SDSUPPORT

Feedback sound, 1514-1521
---------------
	// The duration and frequency for the UI feedback sound.
	// Set these to 0 to disable audio feedback in the LCD menus.
	//
	// Note: Test audio output with the G-Code:
	//  M300 S<frequency Hz> P<duration ms>
	//
	#define LCD_FEEDBACK_FREQUENCY_DURATION_MS 0
	#define LCD_FEEDBACK_FREQUENCY_HZ 0

Smart controller, 1533
---------------
	#define REPRAP_DISCOUNT_SMART_CONTROLLERR

SAV OLEd support, 1637-1643
---------------
	// SAV OLEd LCD module support using either SSD1306 or SH1106 based LCD modules
	//
	//#define SAV_3DGLCD
	#if ENABLED(SAV_3DGLCD)
	  //#define U8GLIB_SSD1306
	  #define U8GLIB_SH1106
	#endif
	
Number of servos, 1920-1927
---------------
	/**
	 * Number of servos
	 *
	 * For some servo-related options NUM_SERVOS will be set automatically.
	 * Set this manually if there are extra servos needing manual control.
	 * Leave undefined or set to 0 to entirely disable the servo subsystem.
	 */
	#define NUM_SERVOS 1 // Servo index starts with 0 for M280 command

pins_GT2560_REV_A_PLUS.h
===============

Bltouch, 31-35
---------------
	#if ENABLED(BLTOUCH)
	  #define SERVO0_PIN  11
	#else
	  #define SERVO0_PIN  11
	#endif

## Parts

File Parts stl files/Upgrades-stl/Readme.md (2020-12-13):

GT2560 A+ housing
----------
GT2560_lid_with_Pi_on_side_and_40mm_fan.stl  

Pi_3_top_with_40mm_fan_and_camera.stl  

Credits to galorin  
http://www.thingiverse.com/thing:2029173

Geetech_GT2560_A_housing.stl

Credits to dariod10 and lukie80  
https://www.thingiverse.com/thing:2248493  

Front LCD mount
----------
LCD-cable-clip.stl  

lcd-support-A.stl  

lcd-support-B.stl

Credits to trepstrer  
https://www.thingiverse.com/thing:2514909  

LCD_cover.stl  

Original Prusa  
https://github.com/prusa3d/Original-Prusa-i3/tree/MK2/Printed-Parts/stl  

160814_LCD_Knob_v2.stl  

Credits to JPgxuAHFR22RQo  
http://www.thingiverse.com/thing:1734712  

Front mounted power switch
----------
GEEETech_Prusa_i3x_Acrylic_-_Front_Power_Switch.stl  

Credits to Hardy90  
http://www.thingiverse.com/thing:1576168  

RPi camera mount
----------
caseBack.stl  

caseFront.stl  

Rpi_camera_bed_mount_for_i3_pro_B.stl  

tiltArm.stl  

Credits to mafrmt00  
https://www.thingiverse.com/thing:2819930  

Single hand bed levelling
----------
EigeneBettHalterungV1.stl  

Credits to TheRealNapalm
http://www.thingiverse.com/thing:1794308

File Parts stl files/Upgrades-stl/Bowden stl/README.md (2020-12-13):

Mount for extruder servo
----------
BOWDEN_EXTRUDER_TOP_PLATE_RHS.stl  

Credits to mike_truebody  

Find the original at https://www.thingiverse.com/thing:2913908  

E3Dv6 fan mount
----------
fan_2.stl  

Radial fan mount for E3Dv6

----------
E3D_v6_BlowerAdapter.stl  

Credits to matt448  

Find the original at https://www.thingiverse.com/thing:1600018  

E3Dv6 part cooler
----------
my part cooler (repaired) meshlab (repaired).stl  

A cleanup of paultsigakis' design  

Find the original at https://www.thingiverse.com/thing:3523424  

E3Dv6 extruder mount and bracket
----------
3d_touch_2.stl  
Bowden_med_3d_touch_bracket.stl  

Could not find original design, sorry...

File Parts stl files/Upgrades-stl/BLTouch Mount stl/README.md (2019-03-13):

Credits to redangel1984  

Find the original at https://www.thingiverse.com/thing:2781315

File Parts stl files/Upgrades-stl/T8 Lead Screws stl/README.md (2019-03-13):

Credits to mike_truebody  

Find the original at https://www.thingiverse.com/thing:2735451

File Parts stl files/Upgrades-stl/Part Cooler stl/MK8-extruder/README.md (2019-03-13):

Credits to redangel1984  

Find the original at https://www.thingiverse.com/thing:2856350

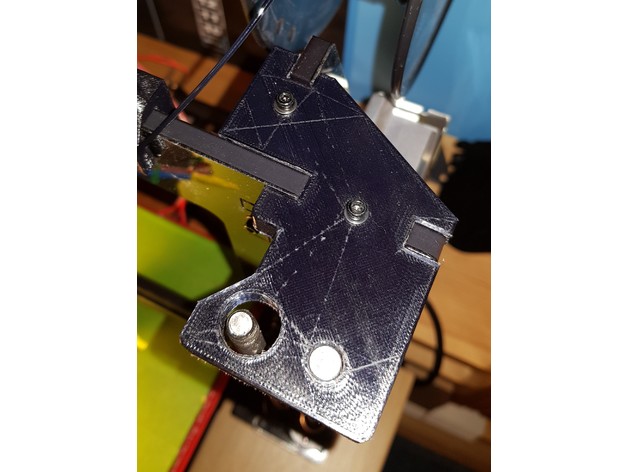
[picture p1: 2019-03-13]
Parts stl files/Upgrades-stl/T8 Lead Screws stl/0c4d6b913d373322894e955787140253_preview_featured.jpg

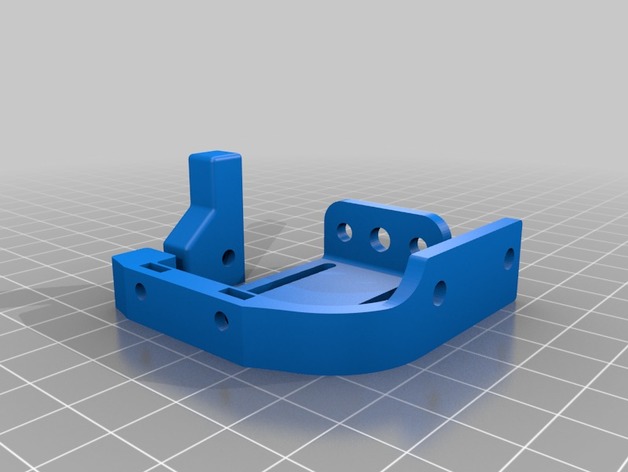
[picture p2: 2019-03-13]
Parts stl files/Upgrades-stl/BLTouch Mount stl/615bfeb8118c8afc70a91da11ffb60c5_preview_featured.jpg

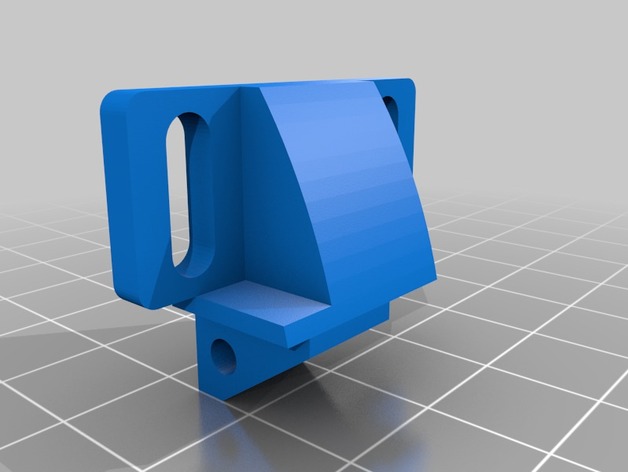
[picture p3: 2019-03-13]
Parts stl files/Upgrades-stl/Part Cooler stl/MK8-extruder/c67abc097c03756e6d8460e441acec06_preview_featured.jpg

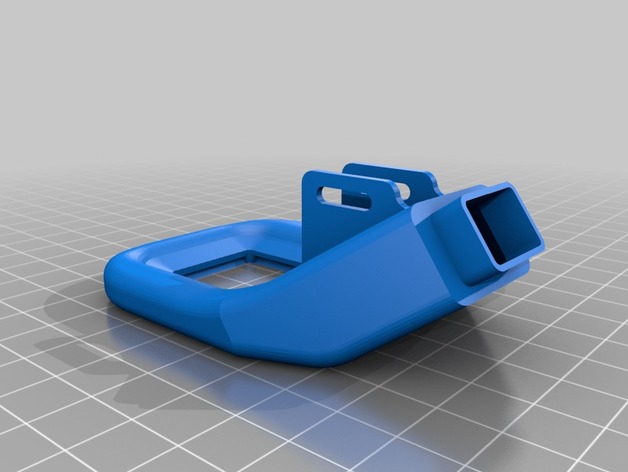
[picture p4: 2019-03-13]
Parts stl files/Upgrades-stl/Part Cooler stl/MK8-extruder/3d76f46f3fab22ff68d1704053df0818_preview_featured.jpg

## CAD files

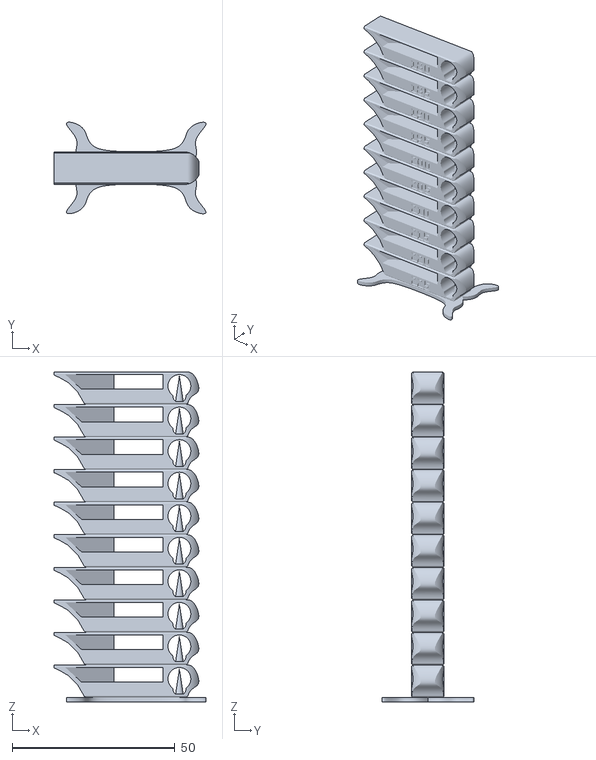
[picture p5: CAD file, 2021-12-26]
Parts stl files/Test stls/SmartTemperatureTower_PLA_180-225.stl
46.7 x 28.2 x 101.4

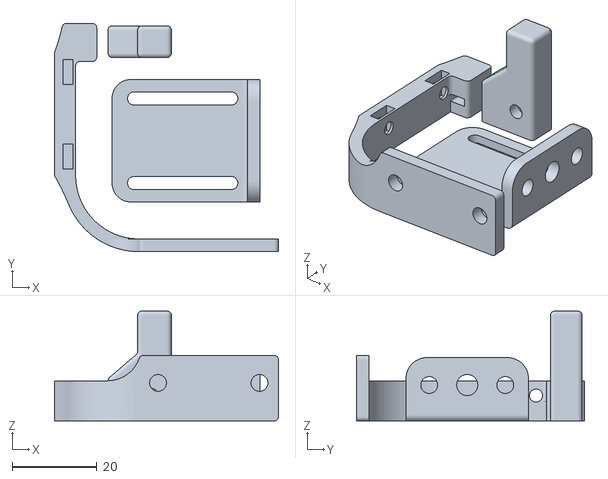
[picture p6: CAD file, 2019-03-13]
Parts stl files/Upgrades-stl/BLTouch Mount stl/3DTouch_Support_for_Geeetech_beta.stl
53.0 x 54.0 x 26.0

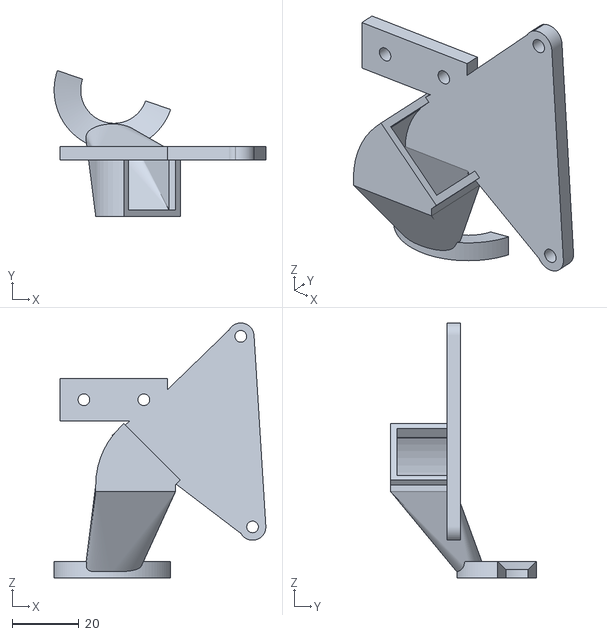
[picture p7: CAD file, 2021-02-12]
Parts stl files/Upgrades-stl/Bowden stl/5015_blower_fanduct-0.15-type3.stl
63.6 x 43.9 x 76.6

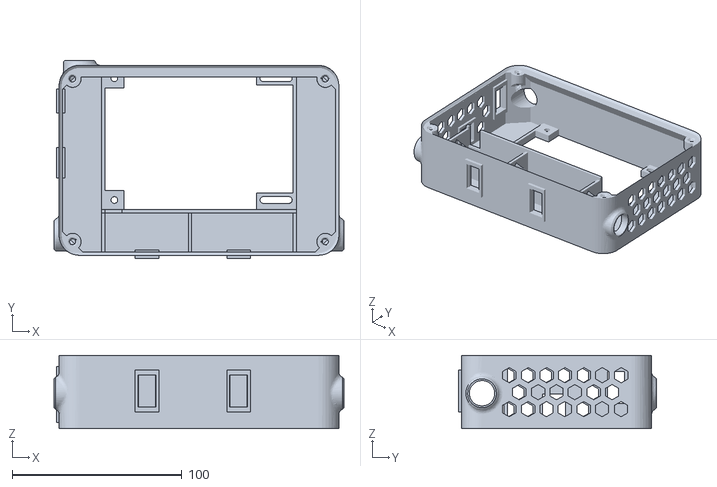
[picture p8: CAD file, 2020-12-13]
Parts stl files/Upgrades-stl/GT2560 A+ housing/Geetech_GT2560_A_housing.stl
171.0 x 117.0 x 43.2

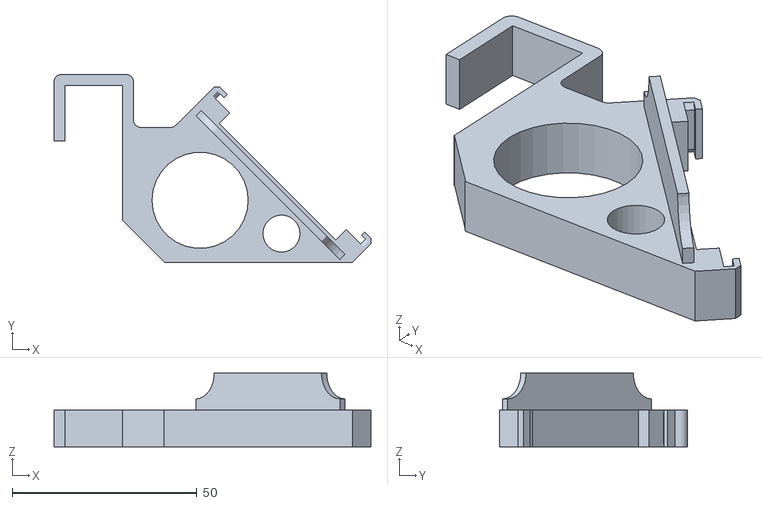
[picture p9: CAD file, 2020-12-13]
Parts stl files/Upgrades-stl/LCD Panel/lcd-support-B.stl
85.7 x 50.8 x 20.0

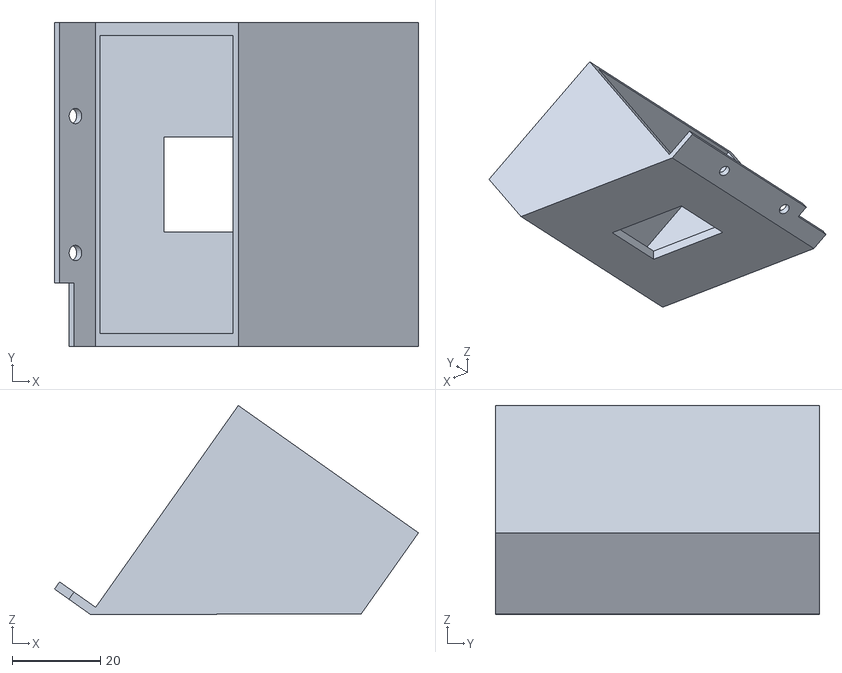
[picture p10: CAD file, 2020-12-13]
Parts stl files/Upgrades-stl/My other upgrades stl/GEEETech_Prusa_i3x_Acrylic_-_Front_Power_Switch.stl
82.5 x 73.5 x 47.4

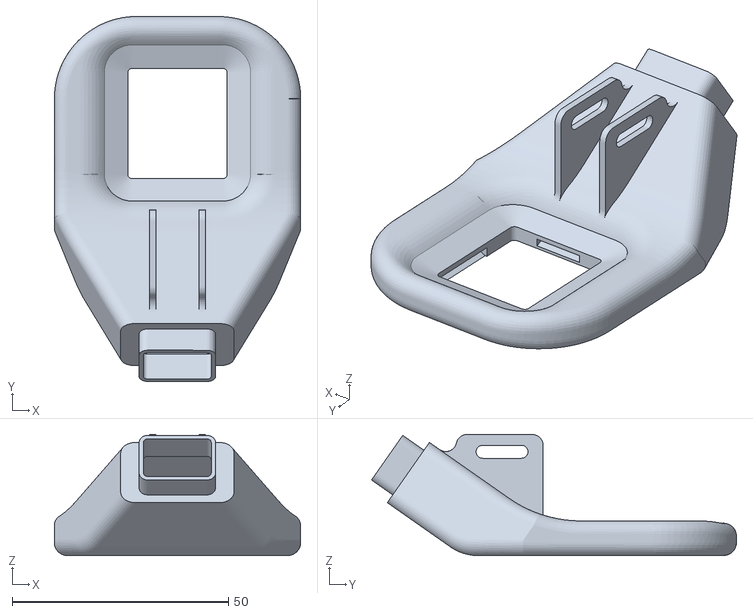
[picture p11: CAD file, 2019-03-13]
Parts stl files/Upgrades-stl/Part Cooler stl/MK8-extruder/Fan_duct.stl
57.0 x 84.4 x 28.0

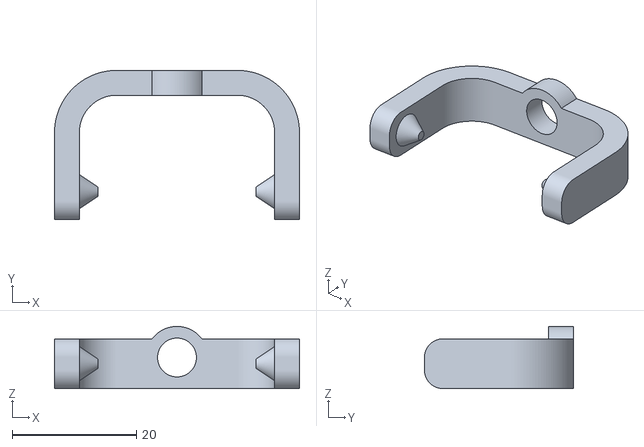
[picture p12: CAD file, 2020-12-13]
Parts stl files/Upgrades-stl/RPi Camera mount/v1/tiltArm.stl
39.4 x 24.0 x 10.0

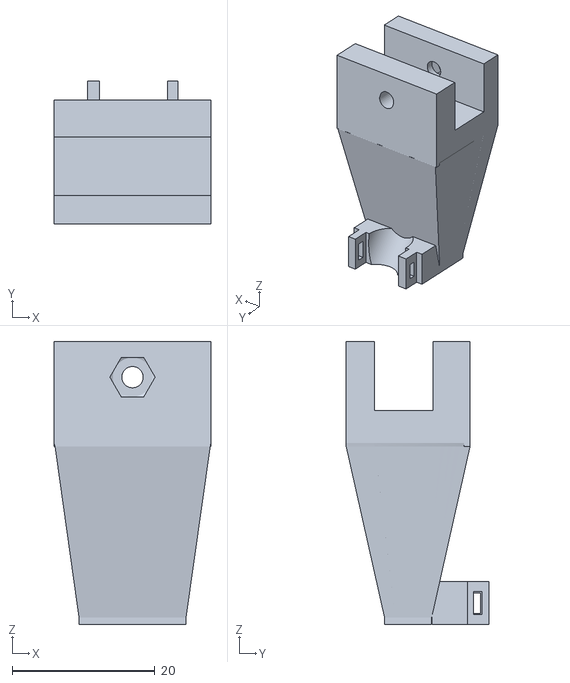
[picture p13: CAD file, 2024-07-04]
Parts stl files/Upgrades-stl/Y-axis/bed_strain_print_on_end.stl
22.0 x 20.0 x 39.7

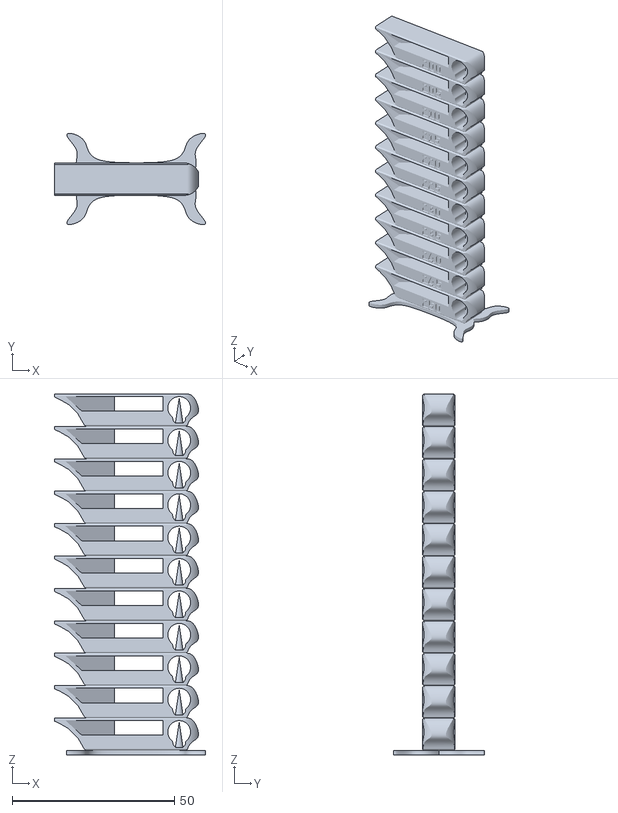
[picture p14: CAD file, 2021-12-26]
Parts stl files/Test stls/SmartTemperatureTower_ABS_200-250.stl
46.7 x 28.2 x 111.4

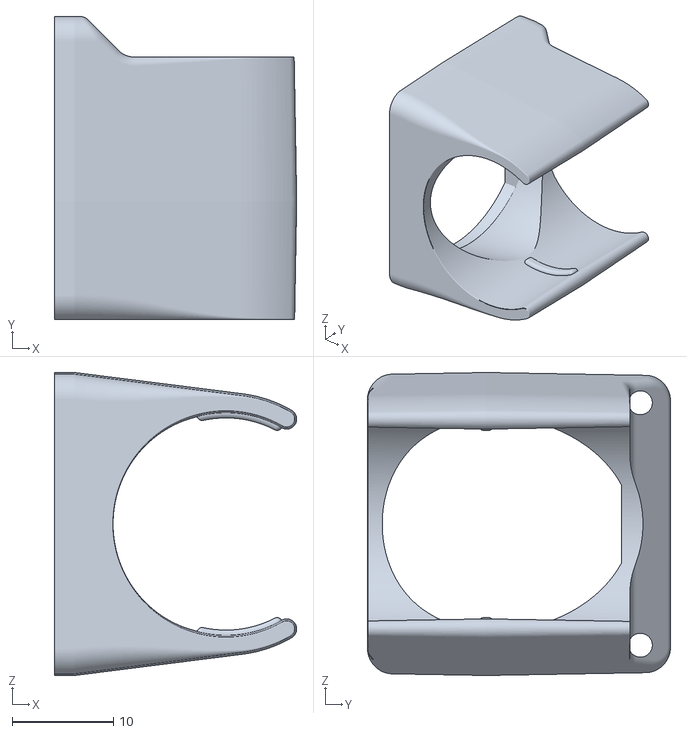
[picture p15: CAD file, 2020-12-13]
Parts stl files/Upgrades-stl/Bowden stl/fan_2.stl
24.0 x 30.0 x 30.0

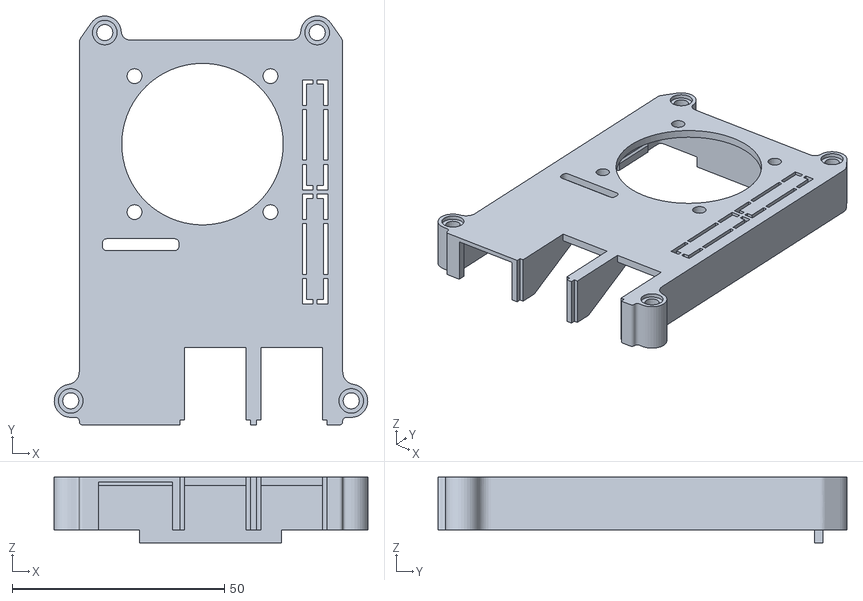
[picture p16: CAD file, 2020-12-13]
Parts stl files/Upgrades-stl/GT2560 A+ housing/Pi_3_top_with_40mm_fan_and_camera.stl
73.8 x 96.2 x 15.5

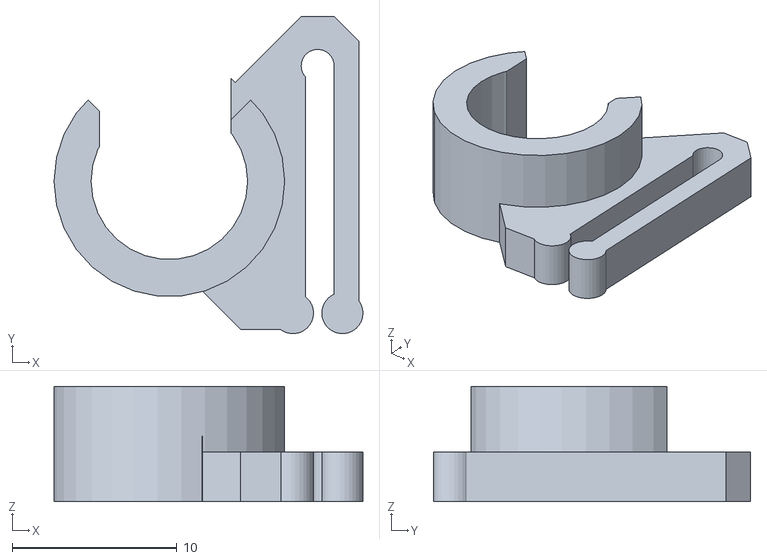
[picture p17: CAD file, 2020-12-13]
Parts stl files/Upgrades-stl/LCD Panel/LCD-cable-clip.stl
18.8 x 19.2 x 7.00

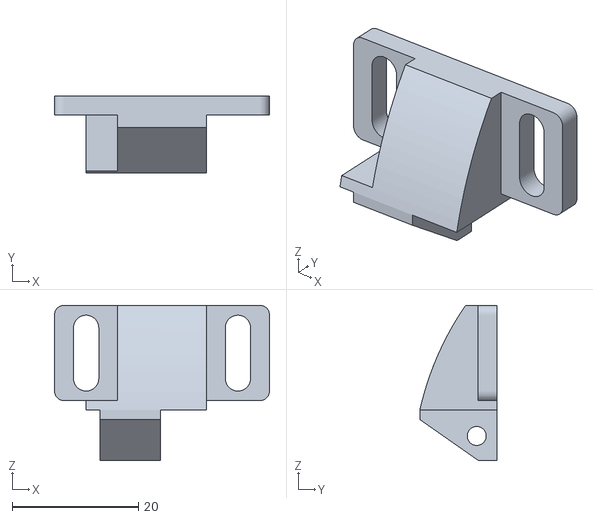
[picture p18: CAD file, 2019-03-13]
Parts stl files/Upgrades-stl/Part Cooler stl/MK8-extruder/Mount.stl
34.0 x 12.2 x 24.6

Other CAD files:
Parts stl files/Upgrades-stl/RPi Camera mount/v1/Rpi_camera_bed_mount_for_i3_pro_B.stl
Parts stl files/Upgrades-stl/Y-axis/bearing_holder.stl
Parts stl files/Test stls/SmartTemperatureTower_PLA_Plus_195-235.stl
Parts stl files/Upgrades-stl/Bowden stl/Bowden_med_3d_touch_bracket.stl
Parts stl files/Test stls/SmartTemperatureTower_PETG_220-265.stl
Parts stl files/Test stls/YACS.stl
Parts stl files/Test stls/YACS_vertical.stl
Parts stl files/Test stls/xyzCalibration_cube.stl
Parts stl files/Upgrades-stl/Bowden stl/3d_touch_2.stl
Parts stl files/Upgrades-stl/Bowden stl/BOWDEN_EXTRUDER_TOP_PLATE_RHS.stl
Parts stl files/Upgrades-stl/Bowden stl/E3D_v6_BlowerAdapter.stl
Parts stl files/Upgrades-stl/GT2560 A+ housing/GT2560_lid_with_Pi_on_side_and_40mm_fan.stl
Parts stl files/Upgrades-stl/LCD Panel/lcd-support-A.stl
Parts stl files/Upgrades-stl/My other upgrades stl/160814_LCD_Knob_v2.stl
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

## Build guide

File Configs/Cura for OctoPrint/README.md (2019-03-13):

#Cura for OctoPrint

OctoPrint slicer uses Cura config files  
However, Cura must be version 15.04 or lower  

Download it here:  
https://ultimaker.com/en/products/ultimaker-cura-software/list  

Or use my configs on this page  

200-65, 0.2mm, 3perims, 40mmps, al
---------------
Extruder temp, C  

	print_temperature = 200
	
Bed temp, C  

	print_bed_temperature = 65

Layer height, mm  

	layer_height = 0.2
	
Wall thickness, mm  

	wall_thickness = 1.2

Support  

	support = None
	
Adhesion:  

	platform_adhesion = None

Print speed, mm/s  

	print_speed = 40

Fill density, %  

	fill_density = 30

Nozzle size, mm  

	nozzle_size = 0.3
	
Filament diameter, mm  

	filament_diameter = 1.75

Start code:  

	M280 P0 S160 ; BLTouch alarm release
	G4 P100 ; delay for BLTouch
	G28 ; home all axes
	G29 ; auto bed leveling
	G1 Z10 F5000 ; lift nozzle
	G92 E0 ; set extruder length to zero

End code:  

	M104 S0 ; turn off extruder heating
	M140 S0 ; turn off bed heating
	G28 X0  ; home X axis
	M84     ; disable motors

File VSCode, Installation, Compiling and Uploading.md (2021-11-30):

# VSCode

Installation instructions are written for a Linux *buntu system.  

Other systems, download from [https://code.visualstudio.com/Download](https://code.visualstudio.com/Download) and follow the guides at [https://code.visualstudio.com/docs/setup/setup-overview](https://code.visualstudio.com/docs/setup/setup-overview).  

## Installation

Download and install keys  
>$ wget -qO- https://packages.microsoft.com/keys/microsoft.asc | gpg --dearmor > packages.microsoft.gpg  
>$ sudo install -o root -g root -m 644 packages.microsoft.gpg /etc/apt/trusted.gpg.d/  
>$ sudo sh -c 'echo "deb [arch=amd64,arm64,armhf signed-by=/etc/apt/trusted.gpg.d/packages.microsoft.gpg] https://packages.microsoft.com/repos/code stable main" > /etc/apt/sources.list.d/vscode.list'  
>$ rm -f packages.microsoft.gpg  

Install prerequisites  
>$ sudo apt install apt-transport-https  

Update and install  
>$ sudo apt update  
>$ sudo apt install code  

## Setup VSCode

Start VSCode from menu, or from cli:  
>$ code  

### Install PlatformIO IDE extension

Click 'Extensions'  
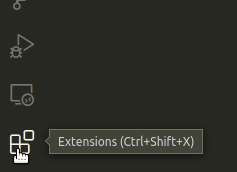
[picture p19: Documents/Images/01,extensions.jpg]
Open Extensions


Search for 'platformio' and then click it  
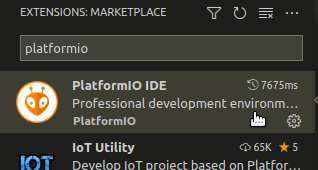
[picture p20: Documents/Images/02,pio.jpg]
Search for PIO


Click 'Install' (in the picture it's already installed)  
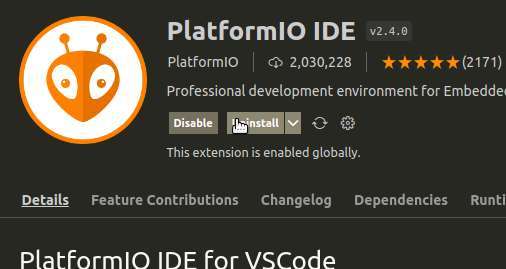
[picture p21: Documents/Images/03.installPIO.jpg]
Install PIO


### Install Auto Build Marlin extension

Again, open 'Extensions' and search for 'marlin'  
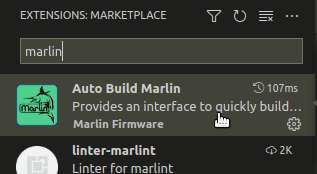
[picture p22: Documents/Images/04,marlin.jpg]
Search for ABM


Click 'Install' (in the picture it's already installed)  
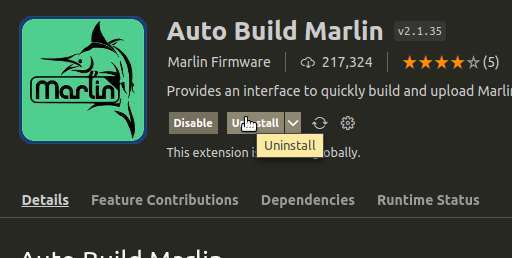
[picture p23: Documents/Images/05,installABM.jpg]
Install ABM


## Get sources

Download sources  
>$ git clone https://github.com/jonsag/Marlin-3D-Printer-Firmware

## Configure Marlin

Open directory with Marlin sources in VSCode  
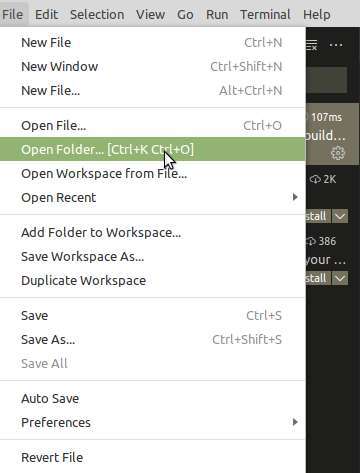
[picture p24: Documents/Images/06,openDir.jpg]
Open directory


Select the directory with the Marlin sources (in this example I'm using 2.0.9.2)  
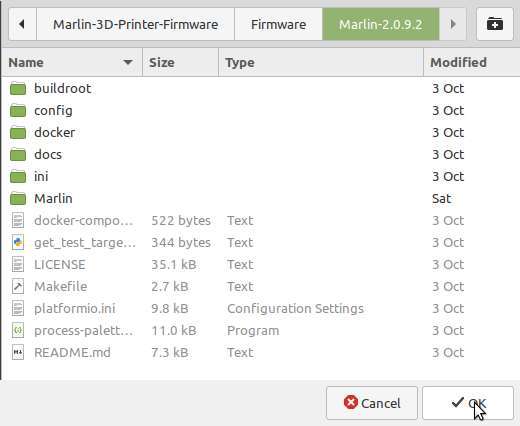
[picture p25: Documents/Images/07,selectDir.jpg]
Select directory


Open and edit the configuration files to your needs  
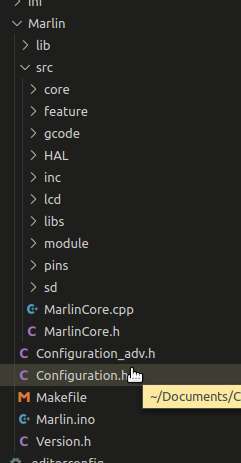
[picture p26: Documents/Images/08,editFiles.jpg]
Edit files


## Build and upload Marlin

Select 'Auto Build Marlin' menu  
Select ABM

Click 'Show ABM Panel'  
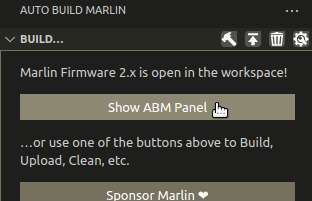
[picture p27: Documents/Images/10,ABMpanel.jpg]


Click 'Build' for 'mega2560'  
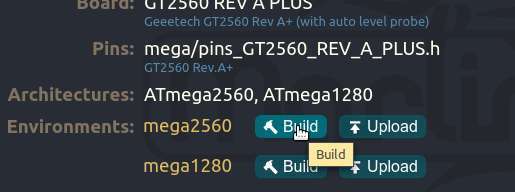
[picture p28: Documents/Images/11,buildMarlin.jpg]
Build Marlin


If all went well you got the firmware binaries at  

    .pio/build/mega2560/firmware.hex  

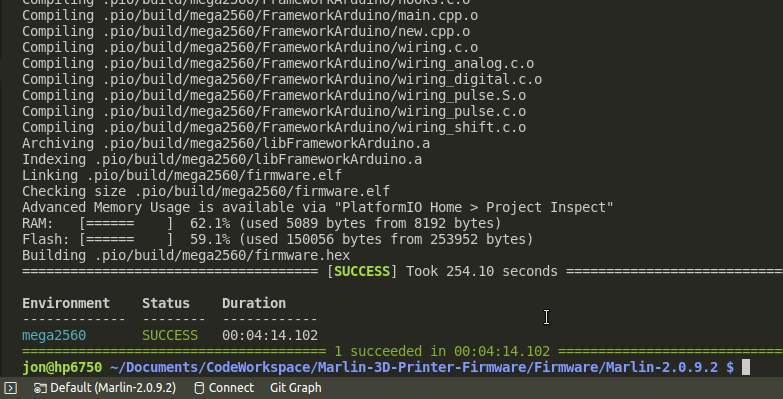
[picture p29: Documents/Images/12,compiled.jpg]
Compilation finished


Save this file for later, or upload it now  
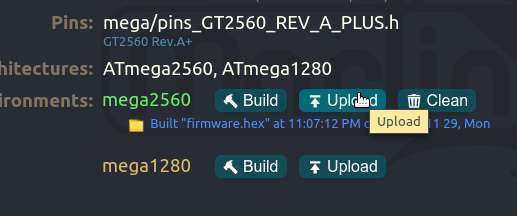
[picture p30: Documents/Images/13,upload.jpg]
Upload firmware


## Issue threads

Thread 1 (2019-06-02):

Sketch fails to compile - Marlin-1.1.9_Geetech_i3_ProB_BLTouch_T8_Lead_Screw

qisback, 2019-06-02:
```
Arduino: 1.8.9 (Windows 10), Board: "Arduino/Genuino Mega or Mega 2560, ATmega2560 (Mega 2560)"

In file included from sketch\MarlinConfig.h:42:0,

                 from sketch\G26_Mesh_Validation_Tool.cpp:27:

SanityCheck.h:947:5: error: static assertion failed: RIGHT_PROBE_BED_POSITION is outside the probe region.

     static_assert(RIGHT_PROBE_BED_POSITION <= MAX_PROBE_X, "RIGHT_PROBE_BED_POSITION is outside the probe region.");

     ^

In file included from sketch\MarlinConfig.h:42:0,

                 from sketch\digipot_mcp4018.cpp:23:

SanityCheck.h:947:5: error: static assertion failed: RIGHT_PROBE_BED_POSITION is outside the probe region.

     static_assert(RIGHT_PROBE_BED_POSITION <= MAX_PROBE_X, "RIGHT_PROBE_BED_POSITION is outside the probe region.");

     ^

In file included from sketch\MarlinConfig.h:42:0,

                 from sketch\I2CPositionEncoder.cpp:31:

SanityCheck.h:947:5: error: static assertion failed: RIGHT_PROBE_BED_POSITION is outside the probe region.

     static_assert(RIGHT_PROBE_BED_POSITION <= MAX_PROBE_X, "RIGHT_PROBE_BED_POSITION is outside the probe region.");

     ^

In file included from sketch\MarlinConfig.h:42:0,

                 from sketch\emergency_parser.cpp:27:

SanityCheck.h:947:5: error: static assertion failed: RIGHT_PROBE_BED_POSITION is outside the probe region.

     static_assert(RIGHT_PROBE_BED_POSITION <= MAX_PROBE_X, "RIGHT_PROBE_BED_POSITION is outside the probe region.");

     ^

exit status 1
In file included from sketch\MarlinConfig.h:42:0,

                 from sketch\printcounter.cpp:23:

SanityCheck.h:947:5: error: static assertion failed: RIGHT_PROBE_BED_POSITION is outside the probe region.

     static_assert(RIGHT_PROBE_BED_POSITION <= MAX_PROBE_X, "RIGHT_PROBE_BED_POSITION is outside the probe region.");

     ^

In file included from sketch\MarlinConfig.h:42:0,

                 from sketch\blinkm.cpp:27:

SanityCheck.h:947:5: error: static assertion failed: RIGHT_PROBE_BED_POSITION is outside the probe region.

     static_assert(RIGHT_PROBE_BED_POSITION <= MAX_PROBE_X, "RIGHT_PROBE_BED_POSITION is outside the probe region.");

     ^

In file included from sketch\MarlinConfig.h:42:0,

                 from sketch\leds.cpp:27:

SanityCheck.h:947:5: error: static assertion failed: RIGHT_PROBE_BED_POSITION is outside the probe region.

     static_assert(RIGHT_PROBE_BED_POSITION <= MAX_PROBE_X, "RIGHT_PROBE_BED_POSITION is outside the probe region.");

     ^

In file included from sketch\MarlinConfig.h:42:0,

                 from sketch\power_loss_recovery.cpp:27:

SanityCheck.h:947:5: error: static assertion failed: RIGHT_PROBE_BED_POSITION is outside the probe region.

     static_assert(RIGHT_PROBE_BED_POSITION <= MAX_PROBE_X, "RIGHT_PROBE_BED_POSITION is outside the probe region.");

     ^

In file included from sketch\MarlinConfig.h:42:0,

                 from sketch\mesh_bed_leveling.cpp:23:

SanityCheck.h:947:5: error: static assertion failed: RIGHT_PROBE_BED_POSITION is outside the probe region.

     static_assert(RIGHT_PROBE_BED_POSITION <= MAX_PROBE_X, "RIGHT_PROBE_BED_POSITION is outside the probe region.");

     ^

In file included from sketch\MarlinConfig.h:42:0,

                 from sketch\twibus.cpp:23:

SanityCheck.h:947:5: error: static assertion failed: RIGHT_PROBE_BED_POSITION is outside the probe region.

     static_assert(RIGHT_PROBE_BED_POSITION <= MAX_PROBE_X, "RIGHT_PROBE_BED_POSITION is outside the probe region.");

     ^

In file included from sketch\MarlinConfig.h:42:0,

                 from sketch\tmc_util.cpp:23:

SanityCheck.h:947:5: error: static assertion failed: RIGHT_PROBE_BED_POSITION is outside the probe region.

     static_assert(RIGHT_PROBE_BED_POSITION <= MAX_PROBE_X, "RIGHT_PROBE_BED_POSITION is outside the probe region.");

     ^

In file included from sketch\MarlinConfig.h:42:0,

                 from sketch\malyanlcd.cpp:44:

SanityCheck.h:947:5: error: static assertion failed: RIGHT_PROBE_BED_POSITION is outside the probe region.

     static_assert(RIGHT_PROBE_BED_POSITION <= MAX_PROBE_X, "RIGHT_PROBE_BED_POSITION is outside the probe region.");

     ^

In file included from sketch\MarlinConfig.h:42:0,

                 from sketch\nozzle.cpp:23:

SanityCheck.h:947:5: error: static assertion failed: RIGHT_PROBE_BED_POSITION is outside the probe region.

     static_assert(RIGHT_PROBE_BED_POSITION <= MAX_PROBE_X, "RIGHT_PROBE_BED_POSITION is outside the probe region.");

     ^

In file included from sketch\MarlinConfig.h:42:0,

                 from sketch\M100_Free_Mem_Chk.cpp:49:

SanityCheck.h:947:5: error: static assertion failed: RIGHT_PROBE_BED_POSITION is outside the probe region.

     static_assert(RIGHT_PROBE_BED_POSITION <= MAX_PROBE_X, "RIGHT_PROBE_BED_POSITION is outside the probe region.");

     ^

In file included from sketch\MarlinConfig.h:42:0,

                 from sketch\digipot_mcp4451.cpp:23:

SanityCheck.h:947:5: error: static assertion failed: RIGHT_PROBE_BED_POSITION is outside the probe region.

     static_assert(RIGHT_PROBE_BED_POSITION <= MAX_PROBE_X, "RIGHT_PROBE_BED_POSITION is outside the probe region.");

     ^

In file included from sketch\MarlinConfig.h:42:0,

                 from sketch\MarlinSerial.cpp:36:

SanityCheck.h:947:5: error: static assertion failed: RIGHT_PROBE_BED_POSITION is outside the probe region.

     static_assert(RIGHT_PROBE_BED_POSITION <= MAX_PROBE_X, "RIGHT_PROBE_BED_POSITION is outside the probe region.");

     ^

In file included from sketch\MarlinConfig.h:42:0,

                 from sketch\neopixel.cpp:27:

SanityCheck.h:947:5: error: static assertion failed: RIGHT_PROBE_BED_POSITION is outside the probe region.

     static_assert(RIGHT_PROBE_BED_POSITION <= MAX_PROBE_X, "RIGHT_PROBE_BED_POSITION is outside the probe region.");

     ^

In file included from sketch\MarlinConfig.h:42:0,

                 from sketch\pca9632.cpp:28:

SanityCheck.h:947:5: error: static assertion failed: RIGHT_PROBE_BED_POSITION is outside the probe region.

     static_assert(RIGHT_PROBE_BED_POSITION <= MAX_PROBE_X, "RIGHT_PROBE_BED_POSITION is outside the probe region.");

     ^

In file included from sketch\MarlinConfig.h:42:0,

                 from sketch\power.cpp:27:

SanityCheck.h:947:5: error: static assertion failed: RIGHT_PROBE_BED_POSITION is outside the probe region.

     static_assert(RIGHT_PROBE_BED_POSITION <= MAX_PROBE_X, "RIGHT_PROBE_BED_POSITION is outside the probe region.");

     ^

In file included from sketch\MarlinConfig.h:42:0,

                 from sketch\Marlin.h:35,

                 from sketch\stepper.cpp:80:

SanityCheck.h:947:5: error: static assertion failed: RIGHT_PROBE_BED_POSITION is outside the probe region.

     static_assert(RIGHT_PROBE_BED_POSITION <= MAX_PROBE_X, "RIGHT_PROBE_BED_POSITION is outside the probe region.");

     ^

In file included from sketch\MarlinConfig.h:42:0,

                 from sketch\SdVolume.cpp:29:

SanityCheck.h:947:5: error: static assertion failed: RIGHT_PROBE_BED_POSITION is outside the probe region.

     static_assert(RIGHT_PROBE_BED_POSITION <= MAX_PROBE_X, "RIGHT_PROBE_BED_POSITION is outside the probe region.");

     ^

In file included from sketch\MarlinConfig.h:42:0,

                 from sketch\enum.h:26,

                 from sketch\parser.h:32,

                 from sketch\parser.cpp:27:

SanityCheck.h:947:5: error: static assertion failed: RIGHT_PROBE_BED_POSITION is outside the probe region.

     static_assert(RIGHT_PROBE_BED_POSITION <= MAX_PROBE_X, "RIGHT_PROBE_BED_POSITION is outside the probe region.");

     ^

In file included from sketch\MarlinConfig.h:42:0,

                 from sketch\SdFile.cpp:29:

SanityCheck.h:947:5: error: static assertion failed: RIGHT_PROBE_BED_POSITION is outside the probe region.

     static_assert(RIGHT_PROBE_BED_POSITION <= MAX_PROBE_X, "RIGHT_PROBE_BED_POSITION is outside the probe region.");

     ^

In file included from sketch\MarlinConfig.h:42:0,

                 from sketch\configuration_store.h:26,

                 from sketch\configuration_store.cpp:47:

SanityCheck.h:947:5: error: static assertion failed: RIGHT_PROBE_BED_POSITION is outside the probe region.

     static_assert(RIGHT_PROBE_BED_POSITION <= MAX_PROBE_X, "RIGHT_PROBE_BED_POSITION is outside the probe region.");

     ^

In file included from sketch\MarlinConfig.h:42:0,

                 from sketch\Sd2Card.cpp:29:

SanityCheck.h:947:5: error: static assertion failed: RIGHT_PROBE_BED_POSITION is outside the probe region.

     static_assert(RIGHT_PROBE_BED_POSITION <= MAX_PROBE_X, "RIGHT_PROBE_BED_POSITION is outside the probe region.");

     ^

In file included from sketch\MarlinConfig.h:42:0,

                 from sketch\hex_print_routines.cpp:23:

SanityCheck.h:947:5: error: static assertion failed: RIGHT_PROBE_BED_POSITION is outside the probe region.

     static_assert(RIGHT_PROBE_BED_POSITION <= MAX_PROBE_X, "RIGHT_PROBE_BED_POSITION is outside the probe region.");

     ^

In file included from sketch\MarlinConfig.h:42:0,

                 from sketch\fwretract.cpp:27:

SanityCheck.h:947:5: error: static assertion failed: RIGHT_PROBE_BED_POSITION is outside the probe region.

     static_assert(RIGHT_PROBE_BED_POSITION <= MAX_PROBE_X, "RIGHT_PROBE_BED_POSITION is outside the probe region.");

     ^

In file included from sketch\MarlinConfig.h:42:0,

                 from sketch\runout.cpp:27:

SanityCheck.h:947:5: error: static assertion failed: RIGHT_PROBE_BED_POSITION is outside the probe region.

     static_assert(RIGHT_PROBE_BED_POSITION <= MAX_PROBE_X, "RIGHT_PROBE_BED_POSITION is outside the probe region.");

     ^

In file included from sketch\MarlinConfig.h:42:0,

                 from sketch\Marlin.h:35,

                 from sketch\Marlin_main.cpp:258:

SanityCheck.h:947:5: error: static assertion failed: RIGHT_PROBE_BED_POSITION is outside the probe region.

     static_assert(RIGHT_PROBE_BED_POSITION <= MAX_PROBE_X, "RIGHT_PROBE_BED_POSITION is outside the probe region.");

     ^

In file included from sketch\MarlinConfig.h:42:0,

                 from sketch\planner_bezier.cpp:30:

SanityCheck.h:947:5: error: static assertion failed: RIGHT_PROBE_BED_POSITION is outside the probe region.

     static_assert(RIGHT_PROBE_BED_POSITION <= MAX_PROBE_X, "RIGHT_PROBE_BED_POSITION is outside the probe region.");

     ^

In file included from sketch\MarlinConfig.h:42:0,

                 from sketch\Max7219_Debug_LEDs.cpp:38:

SanityCheck.h:947:5: error: static assertion failed: RIGHT_PROBE_BED_POSITION is outside the probe region.

     static_assert(RIGHT_PROBE_BED_POSITION <= MAX_PROBE_X, "RIGHT_PROBE_BED_POSITION is outside the probe region.");

     ^

In file included from sketch\MarlinConfig.h:42:0,

                 from sketch\dac_mcp4728.cpp:33:

SanityCheck.h:947:5: error: static assertion failed: RIGHT_PROBE_BED_POSITION is outside the probe region.

     static_assert(RIGHT_PROBE_BED_POSITION <= MAX_PROBE_X, "RIGHT_PROBE_BED_POSITION is outside the probe region.");

     ^

In file included from sketch\MarlinConfig.h:42:0,

                 from sketch\SdFatUtil.cpp:29:

SanityCheck.h:947:5: error: static assertion failed: RIGHT_PROBE_BED_POSITION is outside the probe region.

     static_assert(RIGHT_PROBE_BED_POSITION <= MAX_PROBE_X, "RIGHT_PROBE_BED_POSITION is outside the probe region.");

     ^

In file included from sketch\MarlinConfig.h:42:0,

                 from sketch\ubl.cpp:23:
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
jonsag, 2020-12-15:
Sooo sorry for not noticing this earlier...

Anyway, you probably got this soretd long ago, but it's fixed now.

[57ed901](https://github.com/jonsag/Marlin-3D-Printer-Firmware/commit/57ed901fce8e63e0ef637ca894f78340e1741014)

Closed 2020-12-15.

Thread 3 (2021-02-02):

avr-gcc: error: CreateProcess: No such file or directory - firmware.elf

PrivateRyan94, 2021-02-02:
Hi,

I'm trying to compile the Marlin 2.0.7.2 Project with Arduino 1.8.13 for my GT2560 A+ Printer with BLTouch but I'm getting the avr-gcc error for the x.elf file. I've allready tried to compile th project using Visual Studio Code and I'm getting a simmilar error (with "firmware.elf").

Du you have an idea to fix this?

[arduino.log](https://github.com/jonsag/Marlin-3D-Printer-Firmware/files/5913264/arduino.log)

jonsag, 2021-02-02:
Have you done any changes in the configs as suggested in the [README](https://github.com/jonsag/Marlin-3D-Printer-Firmware/blob/master/README-Marlin-2.0.7.2%2C%20HowTo%20and%20Info.mdl)?

In particular

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

if you don't have the full graphic screen?

I forgot to mention that you must have the [U8glib library](https://www.arduino.cc/reference/en/libraries/u8glib/l) installed, but I see that library mentioned on your log so it looks like you have it.

I really can't tell what your problem is.

Try compiling a [vanilla Marlin](https://github.com/MarlinFirmware/Marlin/archive/2.0.x.zip) or even older versions of it, to rule out anything wrong in my configs.

It's been many years since I compiled anything on a Windoze system, so I have no experience of that,

Compiling on VSCode uses the Arduino IDE installation/compiler (if you use 'Visual Studio Code extension for Arduino'), so it's basically the same thing.
You could try PlatformIO (also available in VSCode), but I haven't tried that myself.

There is a thread on [reprap.org](https://reprap.org/forum/read.php?415,879324,879324) over troubles like yours.
An answer says

> Use vscode with platformio.
>
>Its the only reliable way to compile Marlin under Windows

and he gives a link to [how to do it](https://marlinfw.org/docs/basics/install_platformio_vscode.html).
You could give it a try!

Please report back
/jon

PrivateRyan94, 2021-02-03:
OK, Problem solved. It was an issue with my windows setup ...
Compiling works well on my Ubuntu 20.10 and Arduino 1.8.13.

But I have a new issue...

Send G28
Receive Error:!! STOP called because of BLTouch error - restart with M999
Error:Printer stopped due to errors. Fix the error and use M999 to restart. (Temperature is reset. Set it after restarting)
Error:!! STOP called because of BLTouch error - restart with M999

You have provided these M280 codes in your guide.
Sadly, my printer does nothing after receiving them. He just said "Receive ok" ...

Do you have an idea?

jonsag, 2021-02-03:
How is the BLTouch connected?

If you have the GT2560A+, the BLTouch should be connected on the pins labeled '3D Touch' in this [image](http://www.geeetech.com/wiki/images/thumb/4/40/GT2560A%2B.jpg/700px-GT2560A%2B.jpg).

If you have the older GT2560, and have done the mod described [here](https://www.instructables.com/How-to-Add-Auto-Bed-Leveling-Sensor-to-Geeetech-Pr/), you must also do the firmware changes described there.
This setup is really not covered by my firmware configuration.

If however you have the GT2560A+, I'm thinking you should check your wiring. I really don't know how to measure things up to confirm a correct wiring on the BLTouch. You culd send the M280 commmands and see if any values changes on the connections at all...?

Also I'm hoping you got the original BLTouch from [antclabs](https://www.antclabs.com/).
I have very little faith in the Geeetech clone, since I had two of them myself, and had lots of troubles with both.

Let me know how it works out
/jon

PrivateRyan94, 2021-02-03:
I have the A+ Board and this [BLTouch](https://www.amazon.de/Creality-Verbessertes-Automatische-Bettnivellierungssensoren-Mainboard/dp/B082VSB9VP).

Everything is wired up correctly. I'm using the "3D Touch" and the "Z-Min" pins. I've double checked the pins (+, -, s) but this is correct, too.

With my last firmware, the BLTouch worked fine but I had some other issues in the printing process... So I decided to make a step forward...

Thank you, maybe I'll try it a few more times. I have no idea what's wrong with this printer ... :(

Closed 2021-02-03.

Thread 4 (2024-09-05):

Is the README file for 2.0.9.3 still applicable to 2.1.2.4?

novadaemon1, 2024-09-05:
First thanks for keeping up with this printer. I will be using your firmware settings to resurrect mine,

I have two questions. Is the README file for 2.0.9.3 still applicable to 2.1.2.4 or has anything else changed? Also, do you know the setting to reverse the direction of the X Axis? I have an i3 Pro X and Geeetech mounted the motor in reverse. No firmware I have found has compensated for that; even the default Marlin configs for that printer.

Thanks again.

jonsag, 2024-09-05:
After glancing through that readme, I think it 's still applicable.

The setting for stepper directions are under the comment "// Invert the stepper direction. Change (or reverse the motor connector) if an axis goes the wrong way."

In my configuration.h it's the lines 1695 and forwards.

Good luck
/jon

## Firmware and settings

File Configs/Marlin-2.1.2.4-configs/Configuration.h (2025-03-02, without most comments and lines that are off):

#pragma once
#define CONFIG_EXAMPLES_DIR "config/examples/Geeetech/Prusa i3 Pro B/bltouch"
#define CONFIGURATION_H_VERSION 02010204
#define STRING_CONFIG_H_AUTHOR "jonsag" // Who made the changes.
#define SHOW_BOOTSCREEN
  #define MOTHERBOARD BOARD_GT2560_REV_A_PLUS
#define SERIAL_PORT 0
#define BAUDRATE 250000
#define CUSTOM_MACHINE_NAME "Geeetech i3 Pro B"
#define X_DRIVER_TYPE  A4988
#define Y_DRIVER_TYPE  A4988
#define Z_DRIVER_TYPE  A4988
#define E0_DRIVER_TYPE A4988
#define EXTRUDERS 1
#define DEFAULT_NOMINAL_FILAMENT_DIA 1.75
#define TEMP_SENSOR_0 6
#define TEMP_SENSOR_1 0
#define TEMP_SENSOR_2 0
#define TEMP_SENSOR_3 0
#define TEMP_SENSOR_4 0
#define TEMP_SENSOR_5 0
#define TEMP_SENSOR_6 0
#define TEMP_SENSOR_7 0
#define TEMP_SENSOR_BED 1
#define TEMP_SENSOR_PROBE 0
#define TEMP_SENSOR_CHAMBER 0
#define TEMP_SENSOR_COOLER 0
#define TEMP_SENSOR_BOARD 0
#define TEMP_SENSOR_REDUNDANT 0
#define DUMMY_THERMISTOR_998_VALUE  25
#define DUMMY_THERMISTOR_999_VALUE 100
#if TEMP_SENSOR_IS_MAX_TC(0)
  #define MAX31865_SENSOR_OHMS_0      100 // (Ω) Typically 100 or 1000 (PT100 or PT1000)
  #define MAX31865_CALIBRATION_OHMS_0 430 // (Ω) Typically 430 for Adafruit PT100; 4300 for Adafruit PT1000
#endif
#if TEMP_SENSOR_IS_MAX_TC(1)
  #define MAX31865_SENSOR_OHMS_1      100
  #define MAX31865_CALIBRATION_OHMS_1 430
#endif
#if TEMP_SENSOR_IS_MAX_TC(2)
  #define MAX31865_SENSOR_OHMS_2      100
  #define MAX31865_CALIBRATION_OHMS_2 430
#endif
#if HAS_E_TEMP_SENSOR
  #define TEMP_RESIDENCY_TIME         10  // (seconds) Time to wait for hotend to "settle" in M109
  #define TEMP_WINDOW                  1  // (°C) Temperature proximity for the "temperature reached" timer
  #define TEMP_HYSTERESIS              3  // (°C) Temperature proximity considered "close enough" to the target
#endif
#if TEMP_SENSOR_BED
  #define TEMP_BED_RESIDENCY_TIME     10  // (seconds) Time to wait for bed to "settle" in M190
  #define TEMP_BED_WINDOW              1  // (°C) Temperature proximity for the "temperature reached" timer
  #define TEMP_BED_HYSTERESIS          3  // (°C) Temperature proximity considered "close enough" to the target
#endif
#if TEMP_SENSOR_CHAMBER
  #define TEMP_CHAMBER_RESIDENCY_TIME 10  // (seconds) Time to wait for chamber to "settle" in M191
  #define TEMP_CHAMBER_WINDOW          1  // (°C) Temperature proximity for the "temperature reached" timer
  #define TEMP_CHAMBER_HYSTERESIS      3  // (°C) Temperature proximity considered "close enough" to the target
#endif
#if TEMP_SENSOR_REDUNDANT
  #define TEMP_SENSOR_REDUNDANT_SOURCE    E1  // The sensor that will provide the redundant reading.
  #define TEMP_SENSOR_REDUNDANT_TARGET    E0  // The sensor that we are providing a redundant reading for.
  #define TEMP_SENSOR_REDUNDANT_MAX_DIFF  10  // (°C) Temperature difference that will trigger a print abort.
#endif
#define HEATER_0_MINTEMP   5
#define HEATER_1_MINTEMP   5
#define HEATER_2_MINTEMP   5
#define HEATER_3_MINTEMP   5
#define HEATER_4_MINTEMP   5
#define HEATER_5_MINTEMP   5
#define HEATER_6_MINTEMP   5
#define HEATER_7_MINTEMP   5
#define BED_MINTEMP        5
#define CHAMBER_MINTEMP    5
#define HEATER_0_MAXTEMP 275
#define HEATER_1_MAXTEMP 275
#define HEATER_2_MAXTEMP 275
#define HEATER_3_MAXTEMP 275
#define HEATER_4_MAXTEMP 275
#define HEATER_5_MAXTEMP 275
#define HEATER_6_MAXTEMP 275
#define HEATER_7_MAXTEMP 275
#define BED_MAXTEMP      125
#define CHAMBER_MAXTEMP  60
#define HOTEND_OVERSHOOT 15   // (°C) Forbid temperatures over MAXTEMP - OVERSHOOT
#define BED_OVERSHOOT    10   // (°C) Forbid temperatures over MAXTEMP - OVERSHOOT
#define COOLER_OVERSHOOT  2   // (°C) Forbid temperatures closer than OVERSHOOT
#define PIDTEMP           // See the PID Tuning Guide at https://reprap.org/wiki/PID_Tuning
#define PID_MAX  255      // Limit hotend current while PID is active (see PID_FUNCTIONAL_RANGE below); 255=full current
#define PID_K1     0.95   // Smoothing factor within any PID loop
    #define DEFAULT_Kp  20.27
    #define DEFAULT_Ki   1.59
    #define DEFAULT_Kd 64.77
#define MAX_BED_POWER 255 // limits duty cycle to bed; 255=full current
#define PIDTEMPBED
  #define DEFAULT_bedKp 49.22
  #define DEFAULT_bedKi 9.39
  #define DEFAULT_bedKd 172.04
#define MAX_CHAMBER_POWER 255 // limits duty cycle to chamber heater; 255=full current
  #define PID_FUNCTIONAL_RANGE 10 // If the temperature difference between the target temperature and the actual temperature
#define PREVENT_COLD_EXTRUSION
#define EXTRUDE_MINTEMP 170
#define PREVENT_LENGTHY_EXTRUDE
#define EXTRUDE_MAXLENGTH 200
#define THERMAL_PROTECTION_HOTENDS // Enable thermal protection for all extruders
#define THERMAL_PROTECTION_BED     // Enable thermal protection for the heated bed
#define USE_XMIN_PLUG
#define USE_YMIN_PLUG
#define USE_ZMIN_PLUG
#define ENDSTOPPULLUPS
#define X_MIN_ENDSTOP_INVERTING false // Set to true to invert the logic of the endstop.
#define Y_MIN_ENDSTOP_INVERTING false // Set to true to invert the logic of the endstop.
#define Z_MIN_ENDSTOP_INVERTING false // Set to true to invert the logic of the endstop.
#define I_MIN_ENDSTOP_INVERTING false // Set to true to invert the logic of the endstop.
#define J_MIN_ENDSTOP_INVERTING false // Set to true to invert the logic of the endstop.
#define K_MIN_ENDSTOP_INVERTING false // Set to true to invert the logic of the endstop.
#define U_MIN_ENDSTOP_INVERTING false // Set to true to invert the logic of the endstop.
#define V_MIN_ENDSTOP_INVERTING false // Set to true to invert the logic of the endstop.
#define W_MIN_ENDSTOP_INVERTING false // Set to true to invert the logic of the endstop.
#define X_MAX_ENDSTOP_INVERTING false // Set to true to invert the logic of the endstop.
#define Y_MAX_ENDSTOP_INVERTING false // Set to true to invert the logic of the endstop.
#define Z_MAX_ENDSTOP_INVERTING false // Set to true to invert the logic of the endstop.
#define I_MAX_ENDSTOP_INVERTING false // Set to true to invert the logic of the endstop.
#define J_MAX_ENDSTOP_INVERTING false // Set to true to invert the logic of the endstop.
#define K_MAX_ENDSTOP_INVERTING false // Set to true to invert the logic of the endstop.
#define U_MAX_ENDSTOP_INVERTING false // Set to true to invert the logic of the endstop.
#define V_MAX_ENDSTOP_INVERTING false // Set to true to invert the logic of the endstop.
#define W_MAX_ENDSTOP_INVERTING false // Set to true to invert the logic of the endstop.
#define Z_MIN_PROBE_ENDSTOP_INVERTING false // Set to true to invert the logic of the probe.
#define PRO_B_WITH_LEADSCREW
  #define DEFAULT_AXIS_STEPS_PER_UNIT   { 81.5, 81.5, 400.69, 108 }
#define DEFAULT_MAX_FEEDRATE          { 200, 200, 8, 120 }
#define DEFAULT_MAX_ACCELERATION      { 1000, 1000, 1000, 5000 }
#define DEFAULT_ACCELERATION          1250    // X, Y, Z and E acceleration for printing moves
#define DEFAULT_RETRACT_ACCELERATION  1250    // E acceleration for retracts
#define DEFAULT_TRAVEL_ACCELERATION   3000    // X, Y, Z acceleration for travel (non printing) moves
#define DEFAULT_EJERK    5.0  // May be used by Linear Advance
  #define JUNCTION_DEVIATION_MM 0.03  // (mm) Distance from real junction edge
  #define JD_HANDLE_SMALL_SEGMENTS    // Use curvature estimation instead of just the junction angle
#define S_CURVE_ACCELERATION
#define Z_MIN_PROBE_USES_Z_MIN_ENDSTOP_PIN
#define BLTOUCH
#define NOZZLE_TO_PROBE_OFFSET { 20, 2, -0.9 }
#define PROBING_MARGIN 10
#define PROBING_MARGIN_LEFT 60
#define PROBING_MARGIN_RIGHT 0
#define PROBING_MARGIN_FRONT 0
#define PROBING_MARGIN_BACK 0
#define XY_PROBE_FEEDRATE (133*60)
#define Z_PROBE_FEEDRATE_FAST (20*60)
#define Z_PROBE_FEEDRATE_SLOW (Z_PROBE_FEEDRATE_FAST / 2)
#define MULTIPLE_PROBING 2
#define Z_CLEARANCE_DEPLOY_PROBE   10 // (mm) Z Clearance for Deploy/Stow
#define Z_CLEARANCE_BETWEEN_PROBES  5 // (mm) Z Clearance between probe points
#define Z_CLEARANCE_MULTI_PROBE     5 // (mm) Z Clearance between multiple probes
#define Z_PROBE_LOW_POINT          -2 // (mm) Farthest distance below the trigger-point to go before stopping
#define Z_PROBE_OFFSET_RANGE_MIN -20
#define Z_PROBE_OFFSET_RANGE_MAX 20
#define Z_MIN_PROBE_REPEATABILITY_TEST
#define X_ENABLE_ON 0
#define Y_ENABLE_ON 0
#define Z_ENABLE_ON 0
#define E_ENABLE_ON 0 // For all extruders
#define DISABLE_OTHER_EXTRUDERS   // Keep only the active extruder enabled
#define INVERT_X_DIR true
#define INVERT_Y_DIR true
#define INVERT_Z_DIR false
#define INVERT_E0_DIR true
#define INVERT_E1_DIR true
#define INVERT_E2_DIR true
#define INVERT_E3_DIR true
#define INVERT_E4_DIR true
#define INVERT_E5_DIR true
#define INVERT_E6_DIR true
#define INVERT_E7_DIR true
#define X_HOME_DIR -1
#define Y_HOME_DIR -1
#define Z_HOME_DIR -1
#define X_BED_SIZE 186
#define Y_BED_SIZE 167
#define X_MIN_POS 10
#define Y_MIN_POS -10
#define Z_MIN_POS 0
#define X_MAX_POS (X_MIN_POS+X_BED_SIZE)
#define Y_MAX_POS (-Y_MIN_POS+Y_BED_SIZE)
#define Z_MAX_POS 185
#define MIN_SOFTWARE_ENDSTOPS
  #define MIN_SOFTWARE_ENDSTOP_X
  #define MIN_SOFTWARE_ENDSTOP_Y
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

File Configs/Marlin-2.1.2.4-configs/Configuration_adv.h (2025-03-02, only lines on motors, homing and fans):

#define E0_AUTO_FAN_PIN -1
#define E1_AUTO_FAN_PIN -1
#define E2_AUTO_FAN_PIN -1
#define E3_AUTO_FAN_PIN -1
#define E4_AUTO_FAN_PIN -1
#define E5_AUTO_FAN_PIN -1
#define E6_AUTO_FAN_PIN -1
#define E7_AUTO_FAN_PIN -1
#define CHAMBER_AUTO_FAN_PIN -1
#define COOLER_AUTO_FAN_PIN -1
#define HOMING_BUMP_MM      { 5, 5, 2 }       // (linear=mm, rotational=°) Backoff from endstops after first bump
#define HOMING_BUMP_DIVISOR { 2, 2, 4 }       // Re-Bump Speed Divisor (Divides the Homing Feedrate)
#define MICROSTEP_MODES { 16, 16, 16, 16, 16, 16 } // [1,2,4,8,16]
#define LIN_ADVANCE
    #define ADVANCE_K 0        // (mm) Compression length applying to all extruders
#define ADVANCED_PAUSE_FEATURE
  #define ADVANCED_PAUSE_PURGE_FEEDRATE        3  // (mm/s) Extrude feedrate (after loading). Should be slower than load feedrate.
  #define ADVANCED_PAUSE_PURGE_LENGTH         50  // (mm) Length to extrude after loading.
  #define ADVANCED_PAUSE_RESUME_PRIME          0  // (mm) Extra distance to prime nozzle after returning from park.

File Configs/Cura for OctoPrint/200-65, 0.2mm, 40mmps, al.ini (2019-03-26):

[profile]
layer_height = 0.2
wall_thickness = 1.2
retraction_enable = True
solid_layer_thickness = 1.2
fill_density = 30
nozzle_size = 0.3
print_speed = 40
print_temperature = 200
print_temperature2 = 0
print_temperature3 = 0
print_temperature4 = 0
print_temperature5 = 0
print_bed_temperature = 65
support = None
platform_adhesion = None
support_dual_extrusion = Both
wipe_tower = False
wipe_tower_volume = 15
ooze_shield = False
filament_diameter = 1.75
filament_diameter2 = 0
filament_diameter3 = 0
filament_diameter4 = 0
filament_diameter5 = 0
filament_flow = 100.0
retraction_speed = 40.0
retraction_amount = 4.5
retraction_dual_amount = 16.5
retraction_min_travel = 1.5
retraction_combing = All
retraction_minimal_extrusion = 0.02
retraction_hop = 0.0
bottom_thickness = 0.2
layer0_width_factor = 100
object_sink = 0.0
overlap_dual = 0.15
travel_speed = 120.0
bottom_layer_speed = 20
infill_speed = 60
solidarea_speed = 30
inset0_speed = 25
insetx_speed = 0.0
cool_min_layer_time = 5
fan_enabled = True
skirt_line_count = 3
skirt_gap = 9.0
skirt_minimal_length = 150.0
fan_full_height = 0.5
fan_speed = 100
fan_speed_max = 100
cool_min_feedrate = 10
cool_head_lift = False
solid_top = True
solid_bottom = True
fill_overlap = 15
perimeter_before_infill = False
support_type = Lines
support_angle = 60
support_fill_rate = 15
support_xy_distance = 0.7
support_z_distance = 0.15
spiralize = False
simple_mode = False
brim_line_count = 20
raft_margin = 5.0
raft_line_spacing = 3.0
raft_base_thickness = 0.3
raft_base_linewidth = 1.0
raft_interface_thickness = 0.27
raft_interface_linewidth = 0.4
raft_airgap_all = 0.0
raft_airgap = 0.22
raft_surface_layers = 2
raft_surface_thickness = 0.27
raft_surface_linewidth = 0.4
fix_horrible_union_all_type_a = True
fix_horrible_union_all_type_b = False
fix_horrible_use_open_bits = False
fix_horrible_extensive_stitching = False
plugin_config = (lp1
	.
object_center_x = -1
object_center_y = -1

[alterations]
start.gcode = 
	;Start GCode
	;Sliced at: {day} {date} {time}
	;Basic settings: Layer height: {layer_height} Walls: {wall_thickness} Fill: {fill_density}
	;Print time: {print_time}
	;Filament used: {filament_amount}m {filament_weight}g
	;Filament cost: {filament_cost}
	M280 P0 S160 ; BLTouch alarm release
	G4 P100 ; delay for BLTouch
	G28 ; home all axes
	G29 ; auto bed leveling
	G1 Z10 F5000 ; lift nozzle
	G92 E0 ; set extruder length to zero
	;Start GCode ends
	
end.gcode = 
	;End GCode
	M104 S0 ; turn off extruder heating
	M140 S0 ; turn off bed heating
	G28 X0  ; home X axis
	M84     ; disable motors
	;{profile_string}
	;End GCode ends
	
start2.gcode = ;Sliced at: {day} {date} {time}
	;Basic settings: Layer height: {layer_height} Walls: {wall_thickness} Fill: {fill_density}
	;Print time: {print_time}
	;Filament used: {filament_amount}m {filament_weight}g
	;Filament cost: {filament_cost}
	;M190 S{print_bed_temperature} ;Uncomment to add your own bed temperature line
	;M104 S{print_temperature} ;Uncomment to add your own temperature line
	;M109 T1 S{print_temperature2} ;Uncomment to add your own temperature line
	;M109 T0 S{print_temperature} ;Uncomment to add your own temperature line
	G21        ;metric values
	G90        ;absolute positioning
	M107       ;start with the fan off
	G28 X0 Y0  ;move X/Y to min endstops
	G28 Z0     ;move Z to min endstops
	G1 Z15.0 F{travel_speed} ;move the platform down 15mm
	T1                      ;Switch to the 2nd extruder
	G92 E0                  ;zero the extruded length
	G1 F200 E10             ;extrude 10mm of feed stock
	G92 E0                  ;zero the extruded length again
	G1 F200 E-{retraction_dual_amount}
	T0                      ;Switch to the first extruder
	G92 E0                  ;zero the extruded length
	G1 F200 E10             ;extrude 10mm of feed stock
	G92 E0                  ;zero the extruded length again
	G1 F{travel_speed}
	;Put printing message on LCD screen
	M117 Printing...
end2.gcode = ;End GCode
	M104 T0 S0                     ;extruder heater off
	M104 T1 S0                     ;extruder heater off
	M140 S0                     ;heated bed heater off (if you have it)
	G91                                    ;relative positioning
	G1 E-1 F300                            ;retract the filament a bit before lifting the nozzle, to release some of the pressure
	G1 Z+0.5 E-5 X-20 Y-20 F{travel_speed} ;move Z up a bit and retract filament even more
	G28 X0 Y0                              ;move X/Y to min endstops, so the head is out of the way
	M84                         ;steppers off
	G90                         ;absolute positioning
	;{profile_string}
start3.gcode = ;Sliced at: {day} {date} {time}
	;Basic settings: Layer height: {layer_height} Walls: {wall_thickness} Fill: {fill_density}
	;Print time: {print_time}
	;Filament used: {filament_amount}m {filament_weight}g
	;Filament cost: {filament_cost}
	;M190 S{print_bed_temperature} ;Uncomment to add your own bed temperature line
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

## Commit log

2019-03-12 Moving stuff around
    [Configuration.h, Configuration_adv.h]
2019-03-12 Another readme. Minor update.
    [Configuration.h]
2019-03-13 Centering bed. Added parts
    [3DTouch_Support_for_Geeetech_beta.stl, Configuration.h, Fan_duct.stl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]
2019-03-16 Added marlin 1.1.9
    [Configuration.h, Configuration_adv.h]
2020-12-12 Added Marlin 1.1.8 firmware with bowden T8 leadscrews and vltouch
    [Configuration.h, Configuration_adv.h]
2020-12-13 Added Marlin-2.0.7.2
    [3d_touch_2.stl, BOWDEN_EXTRUDER_TOP_PLATE_RHS.stl, Bowden_med_3d_touch_bracket.stl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]
2020-12-13 Changes after reviewing Marlin github configs
    [Configuration.h]
2020-12-13 Added test stl
    [YACS.stl]
2020-12-13 Changed bed parameters
    [Configuration.h]
2020-12-14 Readme and cleanup
    [Configuration.h]
2020-12-15 Fixes compile error
    [Configuration.h]
2020-12-15 Changed accel n jerk
    [Configuration.h]
2020-12-18 Classic jerk
    [Configuration.h]
2020-12-20 probing margins
    [Configuration.h]
2021-01-01 bilinear levelling
    [Configuration.h]
2021-01-05 Better Readme. Cleaning and moving. Changed config for 2.0.7.2
    [160814_LCD_Knob_v2.stl, 3DTouch_Support_for_Geeetech_beta.stl, 3d_touch_2.stl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]
2021-01-08 Full graphic LCD. Moved stuff around
    [160814_LCD_Knob_v2.stl, 3DTouch_Support_for_Geeetech_beta.stl, 3d_touch_2.stl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]
2021-01-14 added M73
    [Configuration_adv.h, Fan_duct.stl, Mount.stl]
2021-01-15 M73 options
    [Configuration_adv.h]
2021-02-12 config and fanduct
    [5015_blower_fanduct-0.15-type3.stl]
2021-08-02 Marlin-2.0.9.1 (not tested)
    [Configuration.h, Configuration_adv.h]
2021-11-20 Firmware updates
    [Configuration.h, Configuration_adv.h]
2022-01-11 Marlin 2.0.9.3
    [Configuration.h, Configuration_adv.h, esp32.csv]
2022-01-11 Minor config changes (PID bed, M78 etc.)
    [Configuration.h]
2022-06-13 Deleted firmware sources
    [Configuration.h, Configuration_adv.h, esp32.csv]
2022-06-13 Marlin 2.1
    [Configuration.h, Configuration_adv.h]
2022-12-18 Marlin 2.1.2
    [Configuration.h, Configuration_adv.h]
2023-06-17 2.1.2.1, removed precompiles
    [Configuration.h, Configuration_adv.h]
2023-06-17 deleted unnecessary xonfigs
    [Configuration.h, Configuration_adv.h]
2024-06-19 2.0.9.7 configs
    [Configuration.h, Configuration_adv.h]
2024-06-19 2.1.2.4 configs
    [Configuration.h, Configuration_adv.h]
2024-06-30 Configs for Marlin 2.0.9.7 & 2.1.2.4
    [Configuration.h, Configuration_adv.h]
2024-07-04 configs and readme
    [Configuration.h, Configuration_adv.h, bearing_holder.stl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]
2025-01-10 fw 2.1.2.5
    [Configuration.h, Configuration_adv.h]

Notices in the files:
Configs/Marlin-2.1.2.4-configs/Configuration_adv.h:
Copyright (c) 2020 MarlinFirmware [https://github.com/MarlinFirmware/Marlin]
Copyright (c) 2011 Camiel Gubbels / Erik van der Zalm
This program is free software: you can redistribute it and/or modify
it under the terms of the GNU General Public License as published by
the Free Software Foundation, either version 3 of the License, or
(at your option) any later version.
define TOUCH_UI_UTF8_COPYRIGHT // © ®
